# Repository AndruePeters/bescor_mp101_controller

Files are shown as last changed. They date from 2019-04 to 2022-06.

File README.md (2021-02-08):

# Bescor MP101 Controller

Solution to wirelessly control the Bescor MP101 pan and tilt camera motor.
User uses a PS4 controller to control the motor.

## Software Used
* [wiringPi](http://wiringpi.com/)
* [RF24](https://github.com/nRF24/RF24)
* [yaml-cpp](https://github.com/jbeder/yaml-cpp)
* [sfml](https://www.sfml-dev.org/)

## Devices Used
* [Arduino Uno](https://store.arduino.cc/usa/arduino-uno-rev3/) (although, I am using a cheap alternative from China.)
* [Raspberry Pi 3 Model B](https://www.raspberrypi.org/products/raspberry-pi-3-model-b/)
* [nRF24L01+ 2.4GHz](https://www.sparkfun.com/datasheets/Components/SMD/nRF24L01Pluss_Preliminary_Product_Specification_v1_0.pdf)
* [PS4 DualShock 4 Controller](https://www.playstation.com/en-us/explore/accessories/gaming-controllers/dualshock-4/)

# Installation

## Building
The following will actually compile and build the program natively on a Raspberry Pi. Please make sure that all dependencies are installed by running the install.sh script.

```
  (cd into the bescor_mp101_controller directory)
  cmake . -Bbuild
  cmake --build build
```

## Raspberry Pi
* **wiringPi** (dynamically linked since it is preinstalled)
  * wiringPi is installed by default. Follow [the instructions](http://wiringpi.com/download-and-install/) if you need to install it.
* **RF24** (statically linked)
  * `git clone https://github.com/nRF24/RF24`
  * `cd RF24/`
  * `./configure`
  * `sudo make install`
* **yaml-cpp** (statically inked)
  * Follow the instructions [here](https://github.com/jbeder/yaml-cpp).
* **sfml** (need to decide - probably statically linked)
  * If you have Debian then run `sudo apt-get install libsfml-dev`
  * Otherwise, follow the [official guide](https://www.sfml-dev.org/tutorials/2.5/start-linux.php) to manually install it. Version is 2.5 at the time of writing.

## YAML Configuration
Configuration settings for each node.
Example yaml file.
```yaml
camera_nodes:
  # this is the first came
  - channel: 1
    id: 1
    address: 1
    color: BLUE
    power_level: MAX
    data_rate: 250KBPS
    crc_length: DISABLED
    ir_proto: SONY
    zoom_in: 5
    zoom_out: 5
    focus_in: 5
    focus_out: 5

  # add following cameras here
```

#### Channel
Only channel 1 is supported at the moment

#### ID
Acceptable values: 1 - 255
0 is not allowed.

#### Address
Acceptable values: A1, A2, A3, A4, A5
At this point in time, I recommend only using A1

#### Color
Acceptable values:  OFF, BLUE, GREEN, CYAN, RED, MAGENTA, YELLOW, WHITE

#### Power Level
Acceptable values: MIN, LOW, HIGH, MAX

#### Data Rate
Acceptable values: 250KBPS, 1MBPS, 2MBPS
* The lower the speed the further the range. No reason in changing from 250KBPS for this application.

#### CRC Length
Acceptable values: DISABLED, CRC_8, CRC_16

#### IR Protocol
Acceptable values: SONY, NEC
* Hopefully, more will be supported in the future.

#### Zoom In, Zoom Out, Focus In, Focus Out
Any 32 bit number.

## Cross-compile
I created a basic [toolchain](https://github.com/AndruePeters/pi_toolchain) to cross compile for the Raspberry Pi.
The toolchain is simply the standard Raspberry Pi toolchain with precompiled libraries and headers I commonly use for my projects.
I'll write a better cross-compile description once I get the full thing back up.

# Controls
* L1 - cycles camera selection left
* R1 - cycles camera selection right
* L  - Controls the camera.
* R
  * Moving up and down zooms in and out
  * Moving left and right focuses in and out

# Packet Structure
## Motor Packets
`packet.packet_type = 0;`

`packet.payload_used = 3;`

`packet.payload[0] = speed`  This is an integer [0-255]

`packet.payload[1] = x_axis`. Values = {0, 1, 2}. 0 is off, 1 is left, 2 is right.

`packet.payloadp2] = y_axis`. Values = {0, 1, 2}. 0 is off, 1 is down, 2 is up.

## IR Packet
`packet.packet_type = 1;`

`packet.payload_used = 5;`

`packet.payload[0] = IR prot.`

`packet.payload[1 through 4]` is a 32 bit integer code with packet.payload[1] being the MSByte and packet.payload[4] LSByte

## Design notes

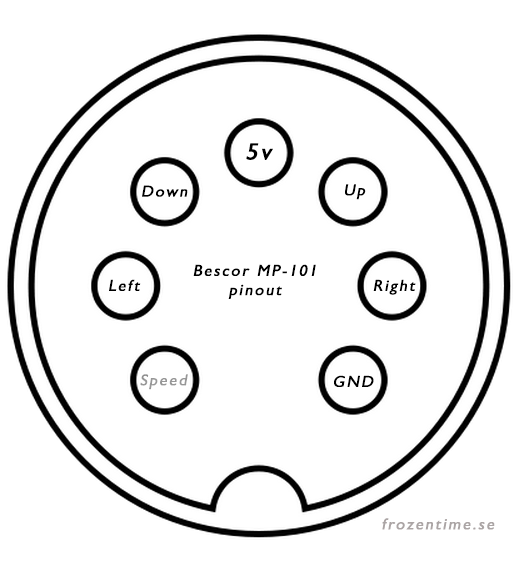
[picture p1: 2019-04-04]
resources/bescor_pinout.png

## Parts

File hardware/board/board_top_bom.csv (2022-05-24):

Comment | Designator | Footprint | LCSC Part #
22 uF | C1 C2 | C0805
220 | R1 | R0805

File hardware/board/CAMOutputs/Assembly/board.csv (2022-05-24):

Qty | Value | Device | Package | Parts | Description | MF | MPN | OC_FARNELL | OC_NEWARK | POPULARITY | SPICEPREFIX
1 |  | ARDUINO_NANO | ARDUINO_NANO | ARDUINO_NANO1 | Arduino Nano V3.0
1 |  | LED5MM | LED5MM | LED1 | LED |  |  |  |  | 93
2 | 22 uF | C-EUC0805 | C0805 | C1, C2 | CAPACITOR, European symbol |  |  |  |  | 88 | C
1 | 220 | R-EU_R0805 | R0805 | R1 | RESISTOR, European symbol |  |  |  |  | 86 | R
1 | MAB7SH | MAB7SH | MAB7SH | X1 | Female CONNECTOR |  |  | unknown | unknown | 0
1 | WIRELESS-NRF24L01 | WIRELESS-NRF24L01 | WIRELESS-NRF24L01 | M1 | 2.4 GHz Wireless Module based on NRF24L01 chip

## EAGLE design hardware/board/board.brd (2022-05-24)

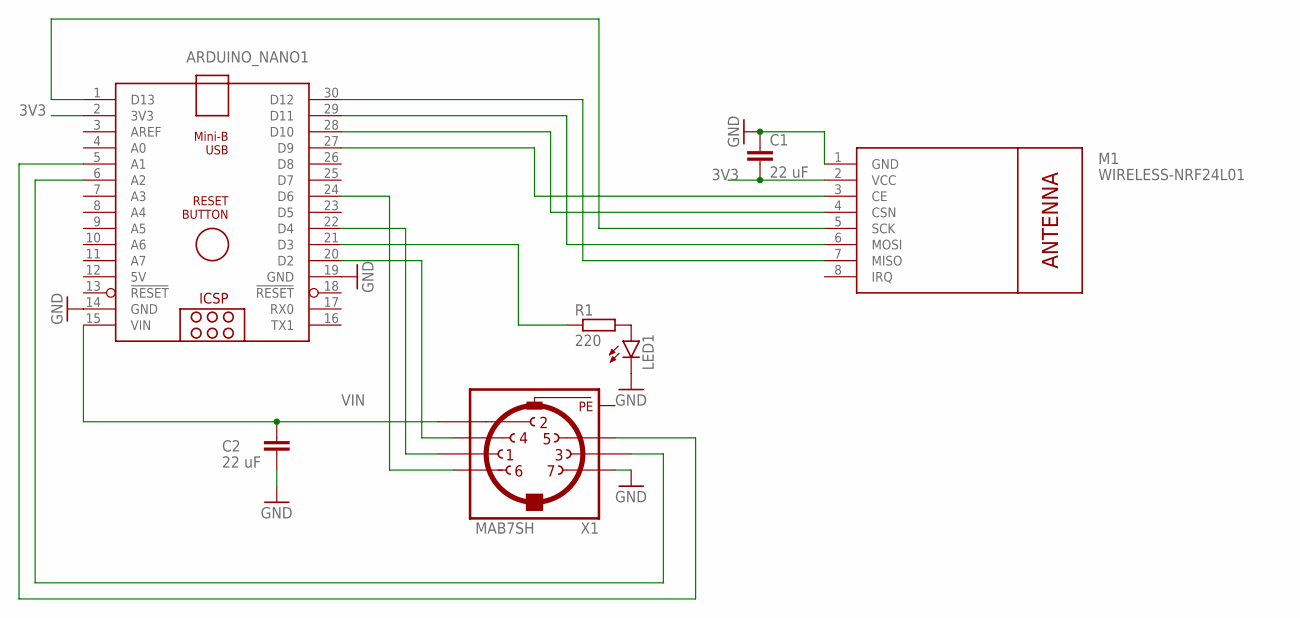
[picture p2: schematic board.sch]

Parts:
ARDUINO_NANO1: ARDUINO_NANO
C1, C2: 22 uF; C0805
LED1: LED5MM
M1: WIRELESS-NRF24L01
R1: 220; R0805
X1: MAB7SH

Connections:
3V3: ARDUINO_NANO1.2 (3V3), C1.2, M1.2 (VCC)
5V: ARDUINO_NANO1.12 (5V)
GND: ARDUINO_NANO1.14 (GND), ARDUINO_NANO1.19 (GND), C1.1, C2.2, LED1.K (C), M1.1 (GND), X1.7
unnamed: ARDUINO_NANO1.1 (D13), M1.5 (SCK)
unnamed: ARDUINO_NANO1.30 (D12), M1.7 (MISO)
unnamed: ARDUINO_NANO1.29 (D11), M1.6 (MOSI)
unnamed: ARDUINO_NANO1.28 (D10), M1.4 (CSN)
unnamed: ARDUINO_NANO1.27 (D9), M1.3 (CE)
unnamed: LED1.A, R1.2
unnamed: ARDUINO_NANO1.21 (D3), R1.1
unnamed: ARDUINO_NANO1.24 (D6), X1.6
unnamed: ARDUINO_NANO1.22 (D4), X1.1
unnamed: ARDUINO_NANO1.5 (A1), X1.5
unnamed: ARDUINO_NANO1.20 (D2), X1.4
unnamed: ARDUINO_NANO1.6 (A2), X1.3
PE: X1.PE, X1.PE@ (PE)
VIN: ARDUINO_NANO1.15 (VIN), C2.1, X1.2

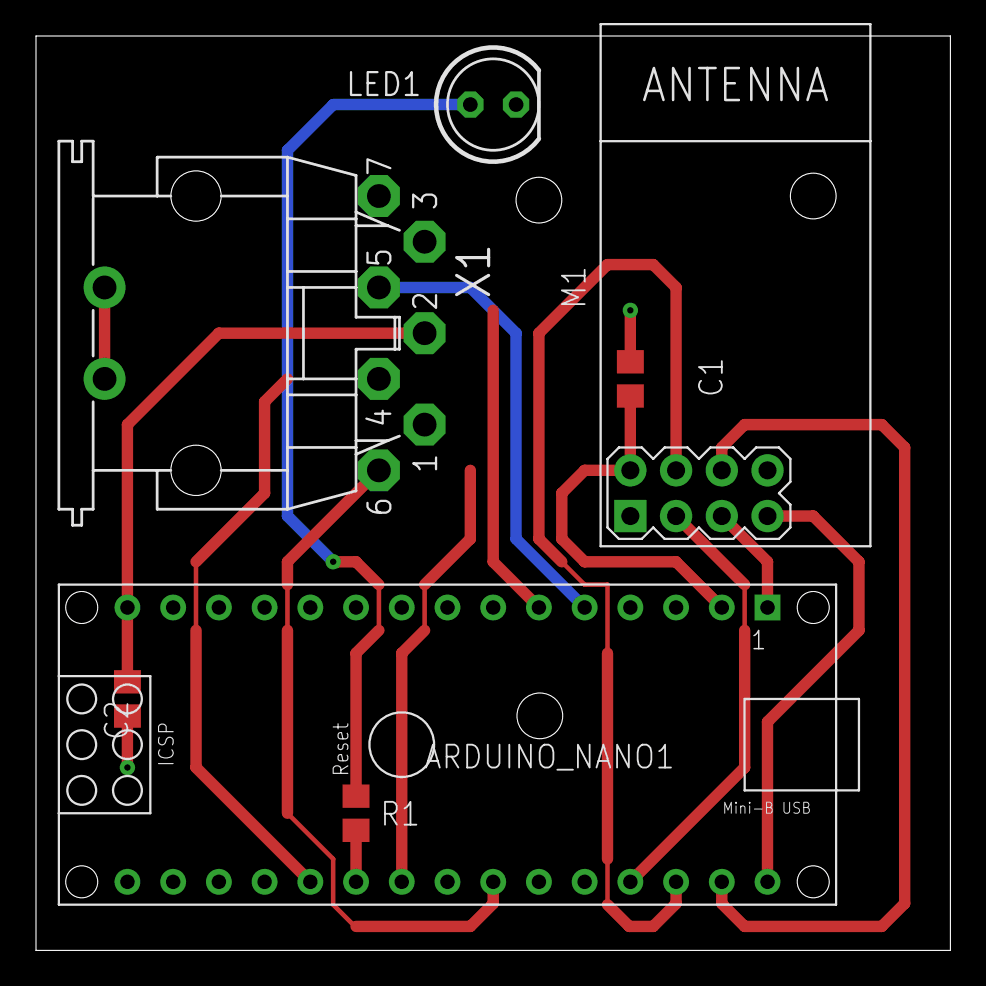
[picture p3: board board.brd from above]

Board: 2 copper layers, 50.8 x 50.8 mm, 7 parts (0 on the bottom side), 16 nets.

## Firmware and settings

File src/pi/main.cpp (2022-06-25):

/*
  main.cpp
  5/1/19
  Andrue Peters

  This is the main file for the program.
  Better description later.
*/
#include <algorithm>
#include <cctype>
#include <chrono>
#include <iostream>
#include <sstream>
#include <thread>
#include <iterator>
#include <csignal>
#include <cstdlib>

#include <RF24/RF24.h>
#include <wiringPi.h>

#include <curses.h>
// specific files projectc++c
#include <node/node.h>
#include <packet/packet.h>
#include <joystick/controller_map.h>
#include <joystick/js.h>

#include <yaml-cpp/yaml.h>
#include <main.h>

#include <spdlog/spdlog.h>

using namespace controller;


// global radio instance
// using wiringPi, so wiringPi pin scheme is also used
// this is equivalent to radio(22, 0) in the generic gettingstarted.cpp
RF24 radio(3, 10);
JS_State js(0);
node_list_t node_list;
const rgb_led_pin_cfg rgb{8, 9, 7}; //in order r, g, b

void ctrlCHandler(sig_atomic_t s) {
    spdlog::error("Ctrl+C was pressed. Gracefully exiting.");
    radio.printDetails();
    exit(1);
}


int main(int argc, char* argv[]) {
    if (argc < 2) {
        spdlog::error("Invalid number of arguments.\nCorrect Use is: {} path/to/config.yaml", argv[0]);
        return EXIT_FAILURE;
    }

    // initialize wiringPi and RF24
    wiringPiSetup();
    rf24_init();
    signal(SIGINT, ctrlCHandler);

    // setup the rgb pins
    pinMode(rgb.red, OUTPUT);
    pinMode(rgb.green, OUTPUT);
    pinMode(rgb.blue, OUTPUT);


    // load config file and store items in node_list
    load_config(argv[1], node_list);
    node_list_it curr_node = node_list.begin();
    node_list_it prev_node = node_list.begin();
    turn_on_leds((*curr_node)->color, rgb);

    while (1) {
        clear();
        process_input(node_list, curr_node);
        refresh();
        std::this_thread::sleep_for(std::chrono::milliseconds(5));
    }

    return 0;
}

/*
 *  Initialize rf24 module to defaults.
 */
void rf24_init() {
    radio.begin();
    //radio.setAutoAck(true);
    //radio.setRetries(10, 15);
    //radio.enableAckPayload();
    //radio.enableDynamicPayloads();
    radio.setChannel(1);
    radio.setPALevel(RF24_PA_MAX);
    radio.openWritingPipe(ADDRESSES[1]);
    radio.openReadingPipe(1, ADDRESSES[0]);
}

/*
 * Configures radio to match node n's properties needed for sending/receiving messages.
 */
void match_node_radio(const nrf2401_prop& n) {
    radio.setDataRate(n.data_rate);
    radio.setCRCLength(n.crc_length);
    radio.setChannel(n.channel);
    set_rf24_write_addr(n.listening_addr);
    radio.stopListening();
}

/*
 *  Sends a packet.
 */
void send_packet(const nrf2401_prop& n, const packet& p) {
    //match_node_radio(n);

    // First, stop listening so we can talk.
    radio.stopListening();
    // attempt to send packet
    if (!radio.write(&p, sizeof(packet))) {

    }
    //radio.stopListening();
    //if (radio.write(&p, sizeof(packet))) {
    //   if (radio.isAckPayloadAvailable()) {
    //        int rec;
    //	    radio.read(&rec, sizeof(rec));
    //   }
    // }
//    radio.writeAckPayload(1, &p, sizeof(packet));
}

/*
 *  Sets the raspberry pi write address to the arduino node listening address
 */
void set_rf24_write_addr(const address_e listening_addr) {
    //radio.openWritingPipe(ADDRESSES[listening_addr]);
    //radio.openReadingPipe(1, ADDRESSES[0]);
    radio.openWritingPipe(ADDRESSES[1]);
    radio.openReadingPipe(1, ADDRESSES[0]);
}

/*
 * Handle and process the input of a joystick
 */
void process_input(node_list_t& nl, node_list_it& it) {
        static int thing = 0;
	if (!js.isConnected()) {
        spdlog::warn("Joystick is not connected. Please connect it to continue.");
        //js.waitUntilConnected();
        while (!js.isConnected()) {
            turn_on_leds(RED, rgb);
            std::this_thread::sleep_for(std::chrono::milliseconds(500));
            turn_on_leds(OFF, rgb);
            js.update();
        }
        spdlog::warn("Joystick has been reconnected!");
        turn_on_leds((*it)->color, rgb);
    }

    // get current joystick state
    js.update();

    if (js.isBtnPressedRaw(DS4::Opt) && js.isBtnPressedRaw(DS4::X)) {
        const auto begin = std::chrono::steady_clock::now();
        auto end = std::chrono::steady_clock::now();
        while (js.isBtnPressedRaw(DS4::Opt) && js.isBtnPressedRaw(DS4::X)) {
            end = std::chrono::steady_clock::now();
            if (std::chrono::duration_cast<std::chrono::seconds>(end - begin).count() >= 10) {
                std::system("sudo shutdown now");
            }
            js.update();
        }
    }

    static packet prevMotorPacket;                                      
    static packet currMotorPacket;            
    static auto prevSent = std::chrono::steady_clock::now();
    auto now = std::chrono::steady_clock::now();
    // let's go ahead and create a motor packet
    create_motor_packet(it, currMotorPacket, js.isBtnPressedRaw(DS4::Sqr));   
                          
     //if something has changed then send a new packet, otherwise don't 
    if (currMotorPacket != prevMotorPacket) {                               
        //print_packet(currMotorPacket);
        send_packet((*it)->rf, currMotorPacket);
        prevSent = now;
	thing=0;
    }

    /// the real issue seems to be power by sending packets too close together
    /// need to get capacitors for the real pi radio to prevent this
    if (thing < 10 && currMotorPacket.payload[1] == 0 && currMotorPacket.payload[2] == 0 && 
                std::chrono::duration_cast<std::chrono::milliseconds>(now - prevSent).count() < 100) {
        send_packet((*it)->rf, currMotorPacket);
        prevSent = now;
	thing++;
    }
    // update previous motor packet.
    prevMotorPacket = currMotorPacket;



    // first check and cycle node
    if (js.isBtnPressed(DS4::L1)) {
	currMotorPacket.payload[0] = currMotorPacket.payload[1] = currMotorPacket.payload[2] = 0;
	send_packet((*it)->rf, currMotorPacket);
        cycle_node_left(nl, it);
        spdlog::info("Current node: {}", (*it)->id);
	thing = false;
    } else if (js.isBtnPressed(DS4::R1)) {
	currMotorPacket.payload[0] = currMotorPacket.payload[1] = currMotorPacket.payload[2] = 0;
	send_packet((*it)->rf, currMotorPacket);
        cycle_node_right(nl, it);
        spdlog::info("Current node: {}", (*it)->id);
	thing = false;
    }



    // don't do the packet stuff with IR yet
    // won't quite work with current Arduino implementation

    // now time to process IR stuff
    // this is all done on the right stick, and L2 must be pressed to toggle
    // between zoom and focus
    // *there's gotta be a better way to factor this logic, check back when not tired
    packet p;
    if (js.getAxisMagnitude(DS4::RS_Y) >= 50.0f) {
        if (js.isBtnPressedRaw(DS4::L2)) {
            // we're going to focus
            if (js.getAxisPos(DS4::RS_Y) >= 50.0f) {
                create_ir_packet(it, p, node_get_focus_in(*it));
            } else if (js.getAxisPos(DS4::RS_Y) <= -50.0f) {
                create_ir_packet(it, p, node_get_focus_out(*it));
            }
        } else {
            // now we're going to zoom zoom zoom
            if (js.getAxisPos(DS4::RS_Y) >= 50.0f) {
                create_ir_packet(it, p, node_get_zoom_in(*it));
            } else if (js.getAxisPos(DS4::RS_Y) <= -50.0f) {
                create_ir_packet(it, p, node_get_zoom_out(*it));
            }
        }
        // if we made it here, then we need to send IR packet
        print_packet(p);
        send_packet((*it)->rf, p);
    }
}

/*
 * Cycle node left
 */
void cycle_node_left(node_list_t& nl, node_list_it& it) {
    if (it == nl.begin()) {
        it = std::prev(nl.end());
    } else {
        --it;
    }

    turn_on_leds((*it)->color, rgb);
    //match_node_radio((*it)->rf);
}

/*
 *  Cycle node right
*/
void cycle_node_right(node_list_t& nl, node_list_it& it) {
    ++it;
    if (it == nl.end()) {
        it = nl.begin();
    }

    turn_on_leds((*it)->color, rgb);
    //match_node_radio((*it)->rf);
}

/*
 *  Creates motor packet.
 */
void create_motor_packet(node_list_it& it, packet& p, bool slow_mode) {
    float x_out, y_out;
    float norm_mag = js.getNormAxis(x_out, y_out, DS4::LS_X, DS4::LS_Y);
    float speed = norm_mag * 255;
    p.packet_type = MOTOR;
    p.payload_used = 3;
    p.id = (*it)->id;
    p.payload[0] = (unsigned) speed;


    if (std::abs(x_out) > 0.010f) {
        p.payload[2] = x_out * 255;
    }

    if (x_out > 0.010f) p.payload[1] = 2;
    else if (x_out < -0.010f) p.payload[1] = 1;
    else p.payload[1] = 0;

    if (std::abs(y_out) > 0.025f) {
        p.payload[3] = y_out * 255;
    }

    if (y_out > 0.025f) p.payload[4] = 2;
    else if (y_out < -0.25f) p.payload[4] = 1;
    else p.payload[2] = 0;

}

/*
 *  Creates the IR packet.
 */
void create_ir_packet(node_list_it& it, packet& p, uint32_t ir_code) {
    p.packet_type = IR;
    p.payload_used = 6;
    p.id = node_get_id(*it);
    p.payload[0] = node_get_ir_prot((*it));
    p.payload[1] = ir_code >> 24;
    p.payload[2] = ir_code >> 16;
    p.payload[3] = ir_code >> 8;
    p.payload[4] = ir_code;
    p.payload[5] = static_cast<uint8_t>(node_get_ir_bit_width((*it)));
}

/*
 *  Dumps packet information to screen;
 */
void print_packet(const packet& p) {
    std::stringstream ss;
    ss << "\nPacket Type: " << (unsigned) p.packet_type
       << "\nPayload Used: " << (unsigned) p.payload_used
       << "\nPacket ID: " << (unsigned) p.id;
    for (int i = 0; i < p.payload_used; ++i) {
        ss << "\nPayload[" << i << "]: " << std::hex << (unsigned) p.payload[i];
    }
    spdlog::info("{}", ss.str());
}

/*
 *  Reads and parses a yaml file (file) and stores nodes in nl
 */
void load_config(std::string file, node_list_t& nl) {
    spdlog::info("Loading configuration file");
    node_prop* np = NULL;
    // verify correct loading of file in future.
    YAML::Node base = YAML::LoadFile(file.c_str());
    YAML::Node arr = base["camera_nodes"];
    spdlog::info("Finished loading configuration file");

    for (auto it = arr.begin(); it != arr.end(); ++it) {
        np = new node_prop;
        node_init(np);
        node_set_id(np, (*it)["id"].as<unsigned>()); // yaml-cpp has issue directly converting to uint8_t
        node_set_color(np, str_to_clr((*it)["color"].as<std::string>()));

        // configure rf properties
        // node_set_power_level(np, str_to_pwr((*it)["power_level"].as<std::string>()));
        // node_set_data_rate(np, str_to_datarate((*it)["data_rate"].as<std::string>()));
        // node_set_crc_length(np, str_to_crclen((*it)["crc_length"].as<std::string>()));
        // node_set_channel(np, (uint8_t)(*it)["channel"].as<unsigned>()); // yaml-cpp has issue converting to uint8_t
        // node_set_address(np, str_to_addr((*it)["address"].as<std::string>()));

        // configure ir properties
        node_set_ir_prot(np, str_to_irprot((*it)["ir_proto"].as<std::string>()));
        node_set_zoom_in(np, (*it)["zoom_in"].as<uint32_t>());
        node_set_zoom_out(np, (*it)["zoom_out"].as<uint32_t>());
        node_set_focus_in(np, (*it)["focus_in"].as<uint32_t>());
        node_set_focus_out(np, (*it)["focus_out"].as<uint32_t>());
        node_set_ir_bit_width(np, (*it)["ir_bit_width"].as<uint32_t>());

        // now store this created node
        nl.push_back(np);
    }
}

/*
 *  Dumps information for the current node.
 */
void print_curr_node(node_list_it& it) {
    std::stringstream ss;
    node_prop* np = (*it);
    ss << "\nColor:\t" << (unsigned) node_get_color(np)
       << "\nID:\t" << (unsigned) node_get_id(np)
       << "\nZoomIn:\t" << node_get_zoom_in(np)
       << "\nZoomOut:\t" << node_get_zoom_out(np)
       << "\nFocus In:\t" << node_get_focus_in(np)
       << "\nFocus Out: " << node_get_focus_out(np)
       << "\n\n";
    addstr(ss.str().c_str());
}


/*
 *  Returns the color_e version of color.
 *  Valid string values: OFF, BLUE, GREEN, CYAN, RED, MAGENTA, YELLOW, WHITE
 */
color_e str_to_clr(std::string color) {
    color_e ret;
    // transform string to upper for comparison
    std::transform(color.begin(), color.end(), color.begin(), ::toupper);
    if (color == "BLUE") {
        ret = BLUE;
    } else if (color == "GREEN") {
        ret = GREEN;
    } else if (color == "CYAN") {
        ret = CYAN;
    } else if (color == "RED") {
        ret = RED;
    } else if (color == "MAGENTA") {
        ret = MAGENTA;
    } else if (color == "YELLOW") {
        ret = YELLOW;
    } else if (color == "WHITE") {
        ret = WHITE;
    } else {
        ret = OFF;
    }

    return ret;
}

/*
 * Converts power to rf24_pa_dbm_e
 * Valid string values: MIN, LOW, HIGH, MAX
 */
rf24_pa_dbm_e str_to_pwr(std::string power) {
    rf24_pa_dbm_e ret;
    std::transform(power.begin(), power.end(), power.begin(), ::toupper);

    if (power == "MIN") {
        ret = RF24_PA_MIN;
    } else if (power == "LOW") {
        ret = RF24_PA_LOW;
    } else if (power == "HIGH") {
        ret = RF24_PA_HIGH;
    } else if (power == "MAX") {
        ret = RF24_PA_MAX;
    } else {
        ret = RF24_PA_ERROR;
    }

    return ret;
}


/*
 * Converts string dr to rf24_datarate_e
 * Valid string values: 250KBPS, 1MBPS, 2MBPS
 */
rf24_datarate_e str_to_datarate(std::string dr) {
    rf24_datarate_e ret;
    std::transform(dr.begin(), dr.end(), dr.begin(), ::toupper);

    if (dr == "250KBPS") {
        ret = RF24_250KBPS;
    } else if (dr == "1MBPS") {
        ret = RF24_1MBPS;
    } else if (dr == "2MBPS") {
        ret = RF24_2MBPS;
    } else {
        ret = RF24_250KBPS;
    }

    return ret;
}

/*
 *  Converts string crc to rf24_crclength_e
 *  Valid string values: DISABLED, CRC_8, CRC_16
 */
rf24_crclength_e str_to_crclen(std::string crc) {
    rf24_crclength_e ret;
    std::transform(crc.begin(), crc.end(), crc.begin(), ::toupper);

    if (crc == "CRC_8") {
        ret = RF24_CRC_8;
    } else if (crc == "CRC_16") {
        ret = RF24_CRC_16;
    } else {
        ret = RF24_CRC_DISABLED;
    }

    return ret;
}

/*
 * Converts string addr to address_e
 * Valid string values: A1, A2, A3, A4, A5
 */
address_e str_to_addr(std::string addr) {
    address_e ret;
    std::transform(addr.begin(), addr.end(), addr.begin(), ::toupper);

    if (addr == "A1") {
        ret = A1_ADDR;
    } else if (addr == "A2") {
        ret = A2_ADDR;
    } else if (addr == "A3") {
        ret = A3_ADDR;
    } else if (addr == "A4") {
        ret = A4_ADDR;
    } else if (addr == "A5") {
        ret = A5_ADDR;
    } else {
        ret = A1_ADDR;
    }
    return ret;
}

/*
 * Convert string ir to ir_prot_e
 * Valid string values: NEC, SONY, RC5, RC6, PANASONIC_OLD, JVC, NECX, SAMSUNG36, GICABLE, DIRECTV, RCMM, CKYM
 */
ir_prot_e str_to_irprot(std::string ir) {
    ir_prot_e ret;
    std::transform(ir.begin(), ir.end(), ir.begin(), ::toupper);

    if (ir == "NEC") {
        ret = IR_NEC;
    } else if (ir == "SONY") {
        ret = IR_SONY;
    } else if (ir == "RC5") {
        ret = IR_RC5;
    } else if (ir == "RC6") {
        ret = IR_RC6;
    } else if (ir == "PANASONIC_OLD") {
        ret = IR_PANASONIC_OLD;
    } else if (ir == "JVC") {
        ret = IR_JVC;
    } else if (ir == "NECX") {
        ret = IR_NECX;
    } else if (ir == "SAMSUNG36") {
        ret = IR_SAMSUNG36;
    } else if (ir == "GICABLE") {
        ret = IR_GICABLE;
    } else if (ir == "DIRECTV") {
        ret = IR_DIRECTV;
    } else if (ir == "RCMM") {
        ret = IR_RCMM;
    } else if (ir == "CKYM") {
        ret = IR_CYKM;
    } else {
        ret = IR_UNKNOWN;
    }

    return ret;
}

void init_display() {
    initscr();
    noecho();
    cbreak();
}

void display_status(node_list_it& it) {
    std::stringstream ss;
    ss << "Current Node: " << (unsigned) node_get_id(*it) << std::endl;
    addstr(ss.str().c_str());
}

void turn_on_leds(bool r, bool g, bool b, const rgb_led_pin_cfg p_cfg) {
    digitalWrite(p_cfg.red, r);
    digitalWrite(p_cfg.green, g);
    digitalWrite(p_cfg.blue, b);
}

void turn_on_leds(color_e clr, const rgb_led_pin_cfg l) {
    switch (clr) {
        case OFF:
            turn_on_leds(0, 0, 0, l);
            break;
        case BLUE:
            turn_on_leds(0, 0, 1, l);
            break;
        case GREEN:
            turn_on_leds(0, 1, 0, l);
            break;
        case CYAN:
            turn_on_leds(0, 1, 1, l);
            break;
        case RED:
            turn_on_leds(1, 0, 0, l);
            break;
        case MAGENTA:
            turn_on_leds(1, 0, 1, l);
            break;
        case YELLOW:
            turn_on_leds(1, 1, 0, l);
            break;
        case WHITE:
            turn_on_leds(1, 1, 1, l);
            break;
        default:
            turn_on_leds(0, 0, 0, l);
            break;
    }
}

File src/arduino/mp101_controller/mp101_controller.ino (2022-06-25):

#include <RF24.h>
#include <SPI.h>
#include <IRLibSendBase.h>
#include <IRLib_P01_NEC.h>
#include <IRLib_P02_Sony.h>
#include <IRLib_P03_RC5.h>
#include <IRLib_P04_RC6.h>
#include <IRLib_P05_Panasonic_Old.h>
#include <IRLib_P06_JVC.h>
#include <IRLib_P07_NECx.h>
#include <IRLib_P08_Samsung36.h>
#include <IRLib_P09_GICable.h>
#include <IRLib_P10_DirecTV.h>
#include <IRLib_P11_RCMM.h>
#include <IRLib_P12_CYKM.h>
#include <IRLibCombo.h>

#include "main.h"
#include "node/node.h"
#include "packet/packet.h"

uint8_t ARDUINO_ID = 0;

const int RF24_CHANNEL = 1;

/// speed, right, left, up, down
const motor_pin_config motor_pins{6, A2, 4, A1, 2};
const radio_pin_config radio_pins{9, 10};
packet input_packet;

RF24 radio(radio_pins.ce, radio_pins.cs);
IRsend ir_send; ///< pin 3

void dump_packet(packet& p) {
    for (int i = 0; i < p.payload_used; ++i) {
        Serial.write("payload[");
        Serial.write((int) i);
        Serial.write("]: ");
        int j = (int) p.payload[i];
        Serial.println(j, HEX);
    }

    Serial.println("\n\n\n");
}

void set_pipe(int id) {
    radio.openWritingPipe(ADDRESSES[0]); // write to the Pi
    radio.openReadingPipe(1, ADDRESSES[1]);
}

void setup() {
    // put your setup code here, to run once:
    config_motor_pins();
    init_rf24();
    Serial.begin(9600);
    Serial.write("Finished setup.\n");
}

void loop() {
    if (radio.available()) {
        radio.read(&input_packet, sizeof(input_packet));
        dump_packet(input_packet);
        //Serial.write("Radio is available.\n");
        if (input_packet.id == ARDUINO_ID) {
            Serial.write("Read packet for this Arduino\n");
            process_packet(input_packet);
        }
    }
}

void erase_packet(packet& p) {
    memset(&p, 0, sizeof(packet));
}

// packet types defined in packet.h
void process_packet(packet& p) {
    switch (p.packet_type) {
        case TELEMETRY:
            break;
        case ADMIN:
            break;
        case MOTOR:
            process_motor_packet(p);
            break;
        case IR:
            process_ir_packet(p);
            break;
        default:
            break;
    }
}

void init_rf24() {
    radio.begin();
    set_pipe(0);
    radio.setChannel(1);
    delay(20); // delay 20ms
    radio.startListening();
}


void process_ir_packet(packet& p) {
    uint32_t reconstructed_ir_code = (static_cast<uint32_t>(p.payload[1]) << 24) |
                                     (static_cast<uint32_t>(p.payload[2]) << 16) |
                                     (static_cast<uint32_t>(p.payload[3]) << 8) |
                                     (static_cast<uint32_t>(p.payload[4]));
    uint8_t protocol = p.payload[0];
    ir_send.send(protocol, reconstructed_ir_code, p.payload[5]);
    erase_packet(p);
}

void config_motor_pins() {
    pinMode(motor_pins.speed, OUTPUT);
    pinMode(motor_pins.right, OUTPUT);
    pinMode(motor_pins.left, OUTPUT);
    pinMode(motor_pins.up, OUTPUT);
    pinMode(motor_pins.down, OUTPUT);
}

/*
  Interprets a motor packet, and sets proper pins.
*/
void process_motor_packet(packet& p) {
    // turn it off before both directional pins are set.
    set_motor_speed(0);

    // set directional values before turning speed back on
    set_motor_speed(p.payload[0]);
    set_motor_tilt(p.payload[3], p.payload[4]);
    set_motor_pan(p.payload[1], p.payload[2]);
}

/*
  Sets the speed of the motor.
  On the actual remote this is done using a sliding pot.
  However, this is using PWM to simulate.

  Valid values are integers [0, 255].
*/
void set_motor_speed(uint8_t speed) {
    analogWrite(motor_pins.speed, speed);
}

void set_motor_up(uint8_t value) {
    analogWrite(motor_pins.up, value);
}

void set_motor_down(uint8_t value) {
    analogWrite(motor_pins.down, value);
}

void set_motor_left(uint8_t value) {
    analogWrite(motor_pins.left, value);
}

void set_motor_right(uint8_t value) {
    analogWrite(motor_pins.right, value);
}


void set_motor_tilt(uint8_t dir, uint8_t value) {
    // set tilt direction
    if (dir == 0) {
        set_motor_down(LOW);
        set_motor_up(LOW);
    } else if (dir == 1) {
        set_motor_down(value);
        set_motor_up(LOW);
    } else if (dir == 2) {
        set_motor_down(LOW);
        set_motor_up(value);
    }
}

void set_motor_pan(uint8_t dir, uint8_t value) {
    if (dir == 0) {
        set_motor_left(LOW);
        set_motor_right(LOW);
    }
    if (dir == 1) {
        set_motor_left(value);
        set_motor_right(LOW);
    } else if (dir == 2) {
        set_motor_left(LOW);
        set_motor_right(value);
    }
}

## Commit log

2019-04-04 Added motor pinout
2019-04-05 Prototypes for node.
2019-05-17 Made sure wiringPi and RF24 are working nicely together
2019-06-02 Calls wiringPi() and radio.begin() in proper order
2019-06-15 Renamed address_e values to be compatible with Arduino IDE
2019-06-15 Initial Arduino commit
2019-06-24 Added ncurses test dialog to see current state of controller
2019-06-24 Added ability to monitor button state and see raw output.
2019-06-28 Functions to create IR and Motor packets
2019-06-28 Switched to using JS_State::getNormAxis()
2019-06-28 Loads information from yaml config. Weird issue with .as<uint8_t>, so changed to .as<unsigned> for getting id
    [main.cpp]
2019-06-28 Added methods to control motor
2019-07-03 Cycles nodes and sends motor packet
2019-07-03 Prototypes for converting string to data type from config.yaml
2019-07-06 Added current directory to link_directories
2019-07-06 Print node
2019-07-06 If joystick not connected, then wait's for input. Replaced sleep with std::this_thread::sleep_for()
    [main.cpp]
2019-07-06 Began main process and fixed up some documentation
    [main.cpp]
2019-07-06 Debug print statements now print to ncurses
2019-07-06 Added some debug statements in process_input() to verify packet is correct
    [main.cpp]
2019-09-23 Gracefully handles Ctrl-C and also fixed bug where it wouldn't communicate
    [main.cpp]
2019-10-28 Working on adding motor and IR funcitnality
2019-10-28 node files because stupid Arduino IDE can't go up folders
2019-10-28 packet fiels becasue stupid Arduino IDE can't go up folders
2019-10-28 function prototypes. will rename
2019-10-30 Added IR_LIB includes, fixed IRsend typo, implemented checking input_packet.id, erase_packet(), init_pins(), removed commented-out code, fixed motor_pin_config in config_motor_pins(), erase_packet() 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
    [mp101_controller.ino]
2019-11-01 Removed ir from led_pin_config, and added function prototypes for turn_on_leds()
2019-11-03 Many changes including adding support to change the arduino node id
2019-11-11 Fixed button bug and changed order colors
    [mp101_controller.ino]
2019-11-16 Switched LED pins and button changes Arduino Id
2019-11-16 Fixed bug where correct packet id wasn't being sent.
    [main.cpp]
2019-11-16 Changed motor delay
2019-11-16 Fixed id being sent over payload
    [main.cpp]
2019-11-29 Changed thread sleep
2019-12-01 blink led when joystick not connected
2019-12-01 Fixed bug causing controller to not shutdown
    [main.cpp]
2019-12-12 Should fix camera stutter when IR commands and motor commands are sent by reducing packets sent
    [main.cpp, mp101_controller.ino]
2021-04-11 circuit template
    [board.sch]
2021-04-12 added schematic and board files
    [board.brd, board.sch]
2021-04-20 added arduino hardware
    [board.brd, bom.csv]
2021-04-21 value update
    [board.brd, board.sch]
2021-05-29 connected 3V3 radio line to the aruino nano
    [board.brd, board.sch]
2021-05-29 Fixed radio pins to be 9 and 10 that reflect the PCB board
    [mp101_controller.ino]
2022-01-09 Update main.cpp
    Commented out config properties that aren't currently in use.
2022-05-24 fixed circuitboard
    [DRILEGEND.CFG, PnP_board_front.csv, board.brd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]
2022-06-24 space out stop commands in case stop command was not received
2022-06-25 pi rf24 max power. changed motor implementation to use pwm when driving pan/tilt pins for better speed control

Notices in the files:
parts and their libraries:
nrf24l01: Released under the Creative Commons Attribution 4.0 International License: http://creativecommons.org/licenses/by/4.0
